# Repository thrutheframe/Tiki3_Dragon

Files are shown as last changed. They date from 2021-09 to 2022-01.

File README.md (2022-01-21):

Gen3 2 Orbiter Dragon 1
# Tiki3_Dragon
<b>Update 21 Nov 2022: </b> \
Till date, I had several requests to design the Tiki3 Dragon mount with a 4010/4020 fan to replace the 3010 fan that cools the hotend. The objective I set on Tiki3 mount system are ease of print, compact, light-weight and efficient. 
\
\
Looking at the side profile of the dragon or V6 hotend, the window needed to push air through is around 25mmx25mm = 625mm sq. For a 4010 the fan diameter is around 38mm which equates to an area of 1134mm sq. For a 3010 fan with a diameter of 28mm it is 616mm sq.
\
\
To install a 4010 fan. The reduction in air path is roughly 2:1. This would mean I have to include proper funneling to reduce the air path which result in the increase the width of the mount, making it not compact. So screw-it and make a short funnel. An axial fan produces low pressure air, when faced with drastic decrease in duct size, back pressure will be a problem. The motor will spin at a slower rpm due to resistance, making efficiency an issue. 
\
\
For a 3010 fan, the air path is roughly 1:1, hence no funneling needed. If there is a need to push more air through the heatbreak fins (using the HF version), a higher rpm fan is recommended ie. Gdstime sells 3010 fan 24V at 12,000 rpm or 8.4V at 20,000 rpm.
\
\
To conclude, I am not going to design Tiki3 Dragon to fit a 4010/4020 fan. 
\
\
<b>Update 12 Nov 2021: </b> This mount is for Orbiter V1.5. There will not be an update of Tiki3_Dragon for Orbiter V2.0. Why? https://github.com/thrutheframe/Tiki3_O2

<b>Update 17 Oct 2021: </b> included fan_duct V2 and added body_top and fanduct_bracket for adxl345. Please note the distance for the mounting holes are 19mm. you will also need to directly solder your wire or use L-pins.
\
\
<b>Update 27 Sep 2021: </b> I have included the step and stl file for the body_base.
\
\
<b>Update 12 Sep 2021: </b> shorter version of cable relief added. reduce by 20mm from the original. This is to prevent the cable from hitting the top bar during tall prints. 
\
\
<b>Update 11 Sep 2021: </b> The existing opening for the heater and thermistor cables enlarge slightly. Do note that if you orientate the heater block is the opposing direction. The opening should not be used. The wire will then run outside the BLT bracket and tied to the cable relief. 
\
\
\
\
<u> BOM of screw:\
-4pcs M3x12 or M3x14 for 3010 fan\
-2pcs M3x12 or M3x14 for fan duct (washer maybe needed as the slot are larger for horizontal adjustments)\
-2pcs M3x8 for body_base to ender carriage\
-2pcs M3x8 for cable relief\
-4pcs M3x8 for BL Bracket\
-1pc  M3x8 for fan duct bracket to body_top\
-2pcs M3x20 for mounting the orbiter and orbiter bracket to the body\
-4pcs M2.5x8 for dragon to Orbiter bracket (it should have come with the dragon)
\
\
BOM\
-3010 fan (Please use the high static pressure version, those that runs at 8500rpm will not push enough air)\
-5015 fan\
\
BLT offset: X= 35.5 Y=0

Please print in high temp filament. PLA and PLA+ will warp at the area closest to the heatblock. I print mine in CF petg. 

I have designed 2 sets; one for self-tapping M3 and another for M3x4x6.3 brass inserts. I recommend using the brass insert version if you can.

There are 2 versions for the mount. adxl and non-adxl. adxl is for Klipper users who want to install adxl1345. If you are a Marlin user, the non adxl version is better.

If printing in ABS or any material that will shrink, please remember to scale while slicing.

Holes on the self tap version are design at 3mm to accomodate for some shrinkage during print which will come to 2.8mm.

mount holes BLT bracket, fan duct bracket are slotted for 1-1.5mm for adjustments 

fanduct has a +-2mm vertical and +-0.7mm horizontal for adjustments 
\
\
  <b>CREDITS:</b>
I have to give credit where credit was due, so here goes: 
  
My wife, for putting up with me as I dive into this insanity of mine. 

20four80five: https://www.thingiverse.com/thing:3354741
For first planting the idea of a side mount cooling fan and front mount part cooling fan

Hangtight: https://www.thingiverse.com/thing:4725293
For using his fan duct in version 3.1 when I was still learning Fusion360 and basing some of the design from him work as they are good.

lorinczroby: https://www.thingiverse.com/thing:4725897
For designing the Orbiter which I used for the direct drive design.

Grabcad community for coming up with all the STEP files that I need ie; 5015, 4010, BL touch, etc

Mellow for sharing with me the STEP file of their NF-Zone hotend. 

Thingiverse and anyone/organisation that I forgot to give credit to.

Please do share your make on Thingiverse: https://www.thingiverse.com/thing:4949727

Gen3 2 Orbiter Dragon 3
Gen3 2 Orbiter Dragon 2
Gen3 2 Orbiter Dragon 4
Gen3 2 Orbiter Dragon 5

<b>FAQs:</b>

Q:Will this design be suitable for the E3D V6 mount?

A: No. This design is specifically rigid mounting the Phaetus Dragon Hotend (and its clones with the same mounting holes), Hence the name. 

Q: If No. Would you be adapt this design for the V6 hotend?

A: Not at the moment. One of the main reasion is that I do not use V6 mount. 

Q: Will this system fit the Sovol/Tronxy/TwoTrees etc etc?

A: Honestly, I would not know as I do not have those printers to work with.

Q: Would you release the STEP file for others to remix your design?

A: I asked this question once and the answer was "if u can remix it, u can design it on your own". He was kindof an asshole, but he was not wrong either. That is why I ended up designing my own mount system. I prefer not to be an asshole. Hence, I would release the STEP files for the body and BL bracket, which will be a good foundation to built your own version/remix. 

Q: Did you test print it in PLA? How did you get even get such specific numbers? "...I find stuff like this very misleading with serious potential to cause damage to printers when people try to do it..." 

A: I try my best to answer questions pertaining to the design. Constructive suggestions and contributions are greatly apperciated. Please be polite and nice.

Q: How accurate is the CFD simulation on your fan duct? Did u consider turbulance of of the 5015? Did u take into account of hotend movement? This design is misleading/shit/rubbish etc etc.

A: My basic CFD simulation of the particles movement (air) is to provide a validation that the air is directed under the nozzle when designing the fan duct. There are many other parameters that I would not know. tbh, it's a fanduct for 3D printer, not a cooling system of a nuclear plant... so take a chill pill and dun go karen/kevin on me. 

Q: Why do you add a heat sink to your motor? it is counter-productive as it add weight? 

A: Simple. I like it. 

Q: Why it is called Tiki3

A: Tiki was the name of our family dog. He passed away several years ago and we still miss him dearly. So I named this system after him. 

<b>Contributions</b>\
 My 3D printing hobby is running on Fun-Funds which is usually in fumes state. Contribution to this funds are from small print jobs, servicing 3D printers and the once-in-a-blue-moon tip to my paypal.me account. If you like using this system and would like to thanks me, a $2 coffee tip will be greatly appreciated (I like coffee). Thank you. https://www.paypal.com/paypalme/shannonheng

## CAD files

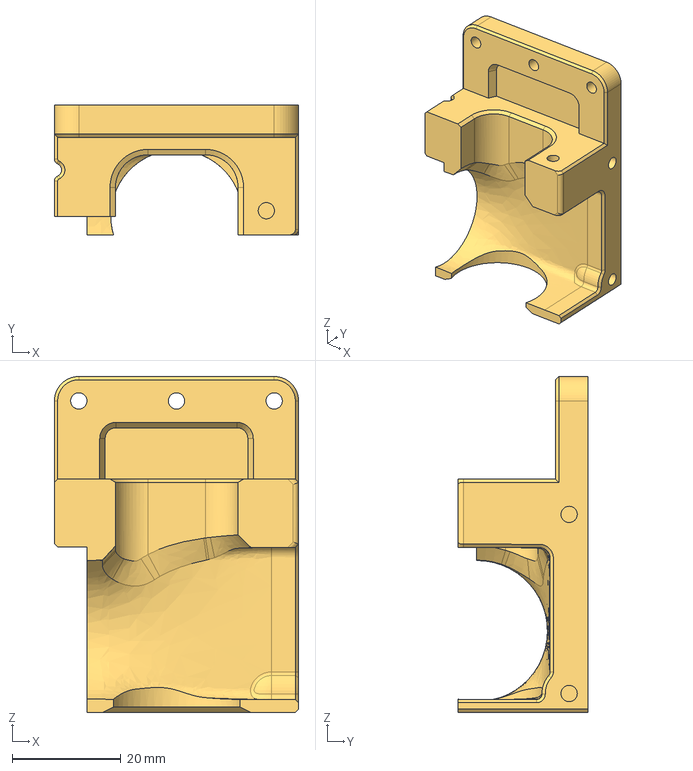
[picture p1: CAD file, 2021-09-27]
Body base STEP files/Tiki3 Dragon Body_base.step
45.0 x 24.0 x 61.9 mm

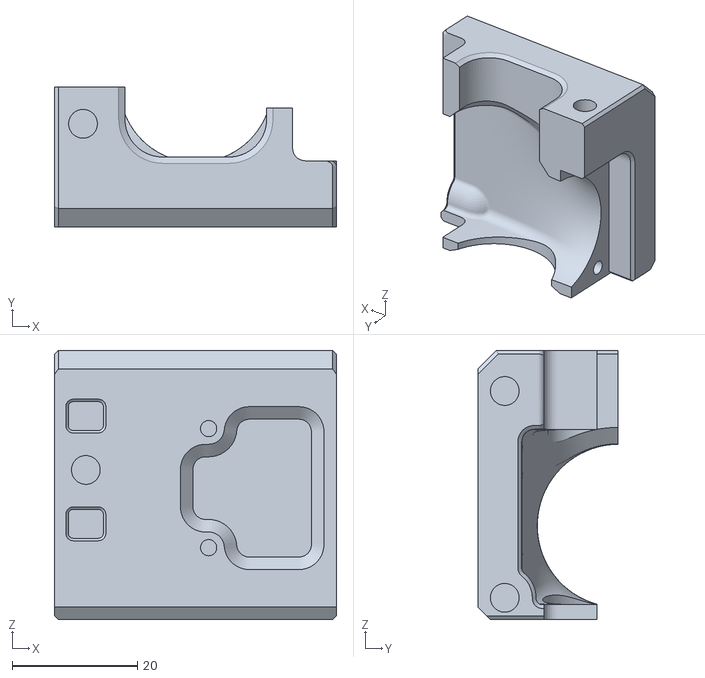
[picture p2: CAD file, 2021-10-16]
Tiki3 V3.2 Dragon brass insert/Brass insert Tiki3 Dragon Body_top adxl.stl
45.0 x 22.4 x 43.0

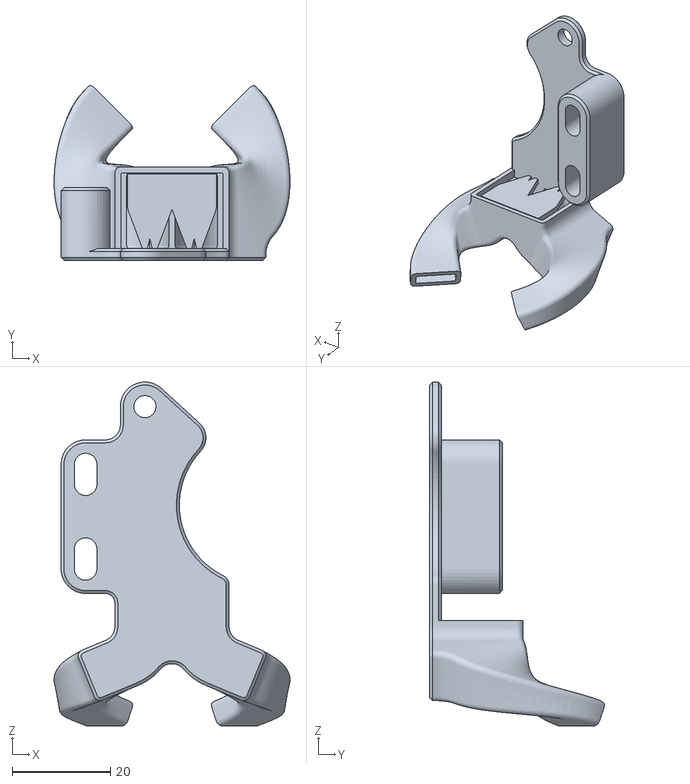
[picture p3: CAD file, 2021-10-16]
Tiki3 V3.2 Dragon other parts/Tiki3 Dragon Fan_duct V2.stl
47.9 x 35.5 x 69.9

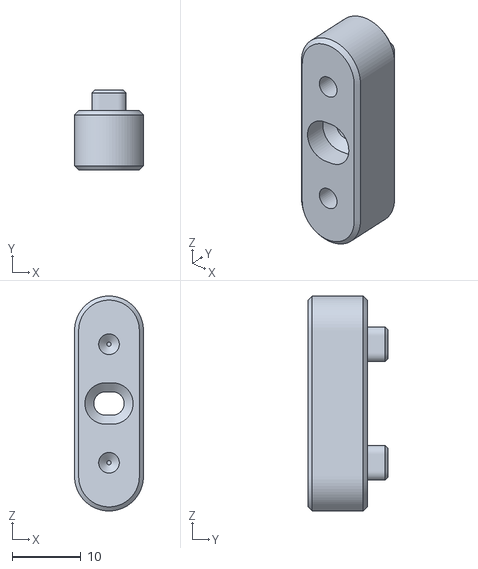
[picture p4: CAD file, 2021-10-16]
Tiki3 V3.2 Dragon self_tap/Tiki3 Dragon Fanduct bracket adxl.stl
10.00 x 11.6 x 31.2

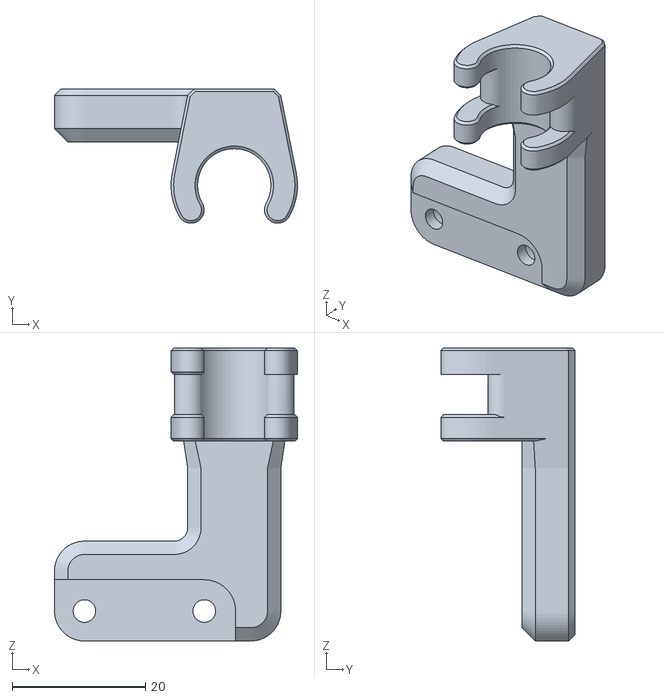
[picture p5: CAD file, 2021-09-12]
Tiki3 V3.2 Dragon other parts/Tiki3 Dragon Cable relief short ver.stl
36.5 x 20.2 x 44.0

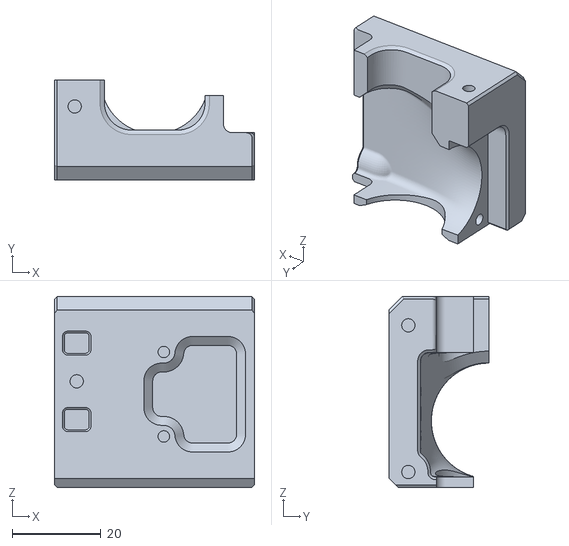
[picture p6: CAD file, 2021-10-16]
Tiki3 V3.2 Dragon self_tap/Tiki3 Dragon Body_top adxl.stl
45.0 x 22.4 x 43.0

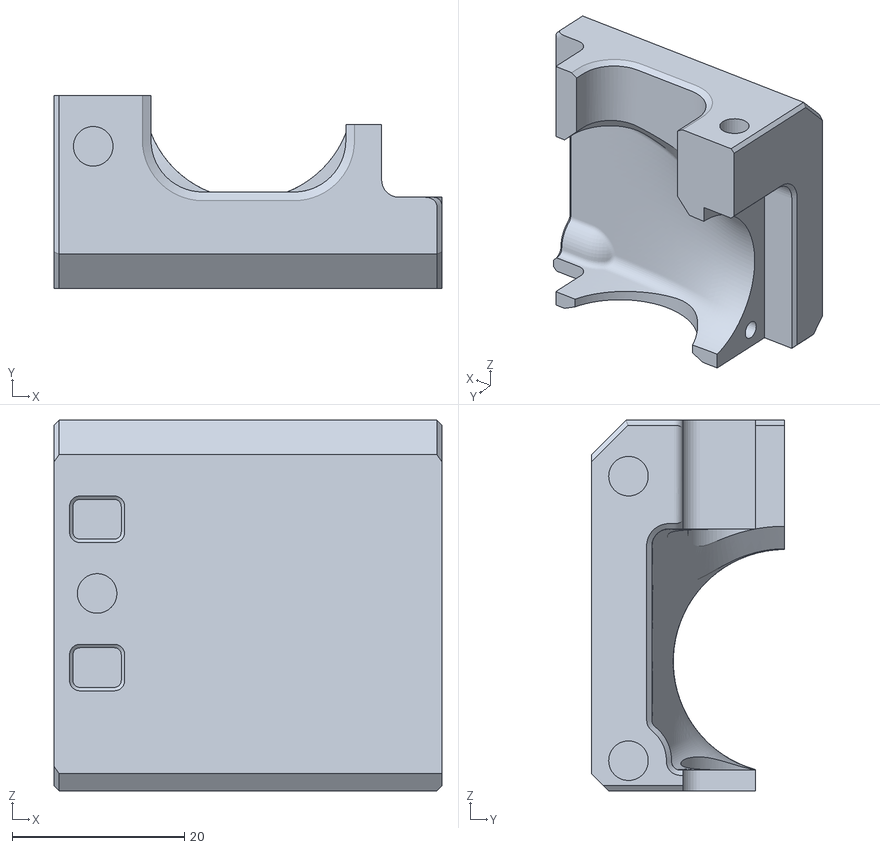
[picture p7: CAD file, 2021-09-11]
Tiki3 V3.2 Dragon brass insert/Brass insert Tiki3 Dragon Body_top.stl
45.0 x 22.4 x 43.0

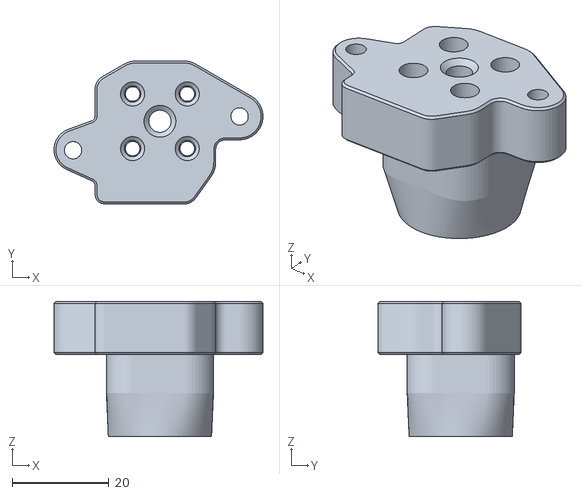
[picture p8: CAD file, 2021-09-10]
Tiki3 V3.2 Dragon other parts/Tiki3 Dragon Orbiter bracket.stl
43.3 x 29.6 x 28.0

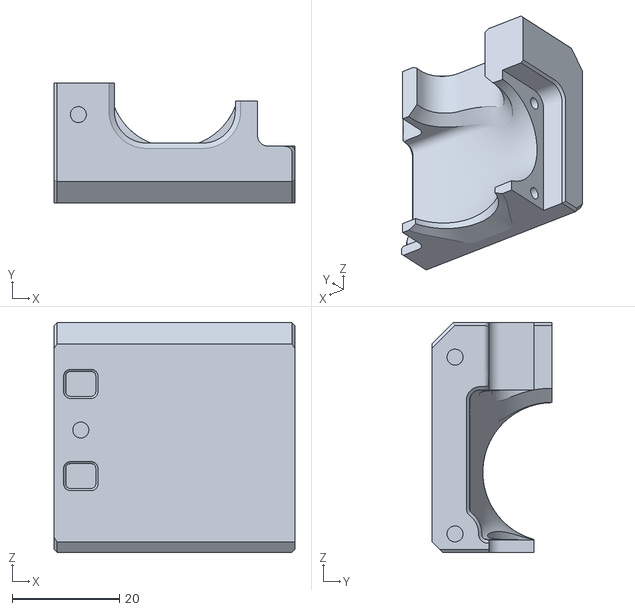
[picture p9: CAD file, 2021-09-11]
Tiki3 V3.2 Dragon self_tap/Tiki3 Dragon Body_top.stl
45.0 x 22.4 x 43.0

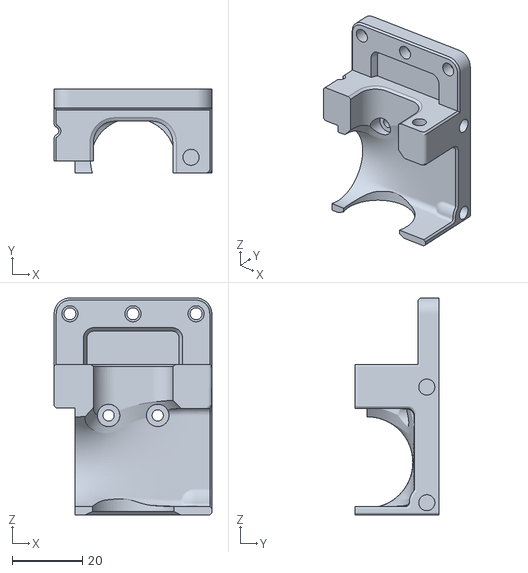
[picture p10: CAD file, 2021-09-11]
Tiki3 V3.2 Dragon brass insert/Brass insert Tiki3 Dragon Body_base.stl
45.0 x 24.0 x 61.9

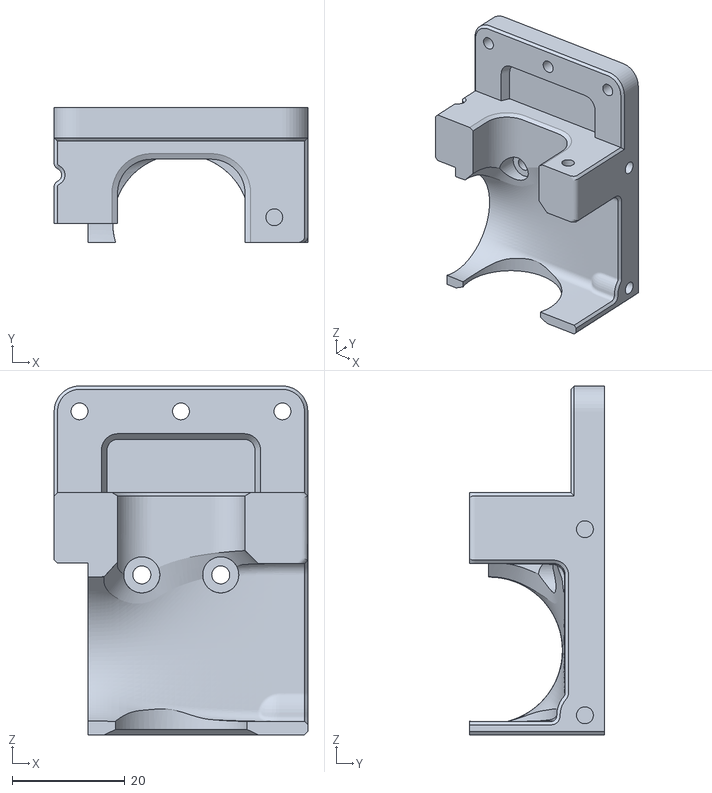
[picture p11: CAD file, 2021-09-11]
Tiki3 V3.2 Dragon self_tap/Tiki3 Dragon Body_base.stl
45.0 x 24.0 x 61.9

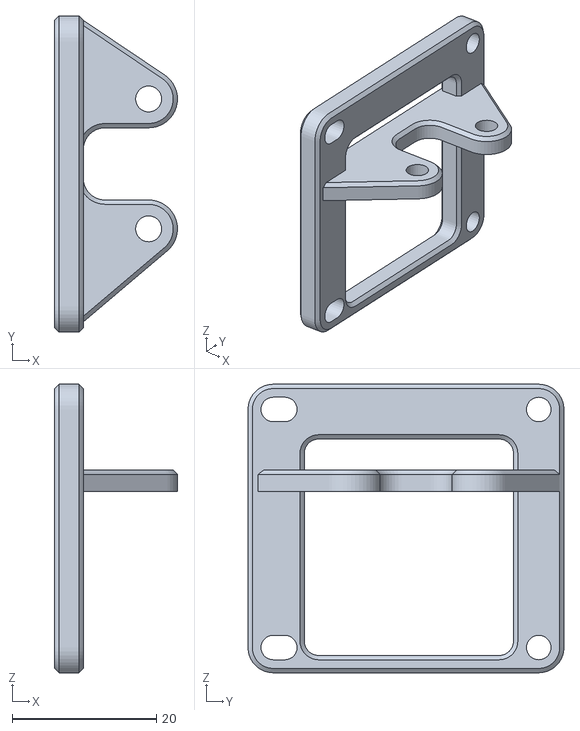
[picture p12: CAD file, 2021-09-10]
Tiki3 V3.2 Dragon other parts/Tiki3 Dragon BLT bracket.stl
17.0 x 43.8 x 40.0

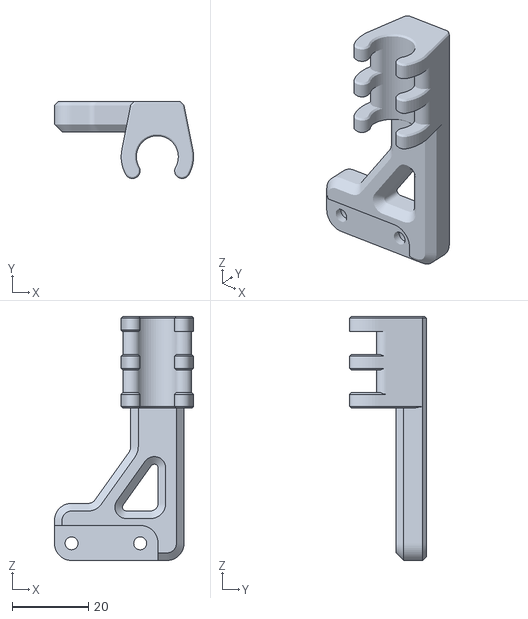
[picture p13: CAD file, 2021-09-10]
Tiki3 V3.2 Dragon other parts/Tiki3 Dragon Cable relief.stl
36.5 x 20.2 x 64.0

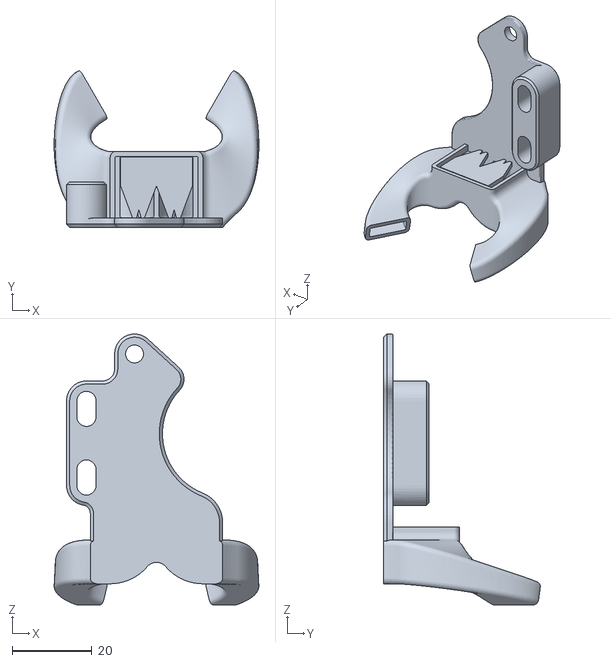
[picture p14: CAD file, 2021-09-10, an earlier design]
Tiki3 V3.2 Dragon other parts/Tiki3 Dragon Fan_duct.stl
51.3 x 39.3 x 67.9

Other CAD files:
Tiki3 V3.2 Dragon brass insert/Brass insert Tiki3 Dragon Fanduct bracket adxl.stl
Tiki3 V3.2 Dragon brass insert/Brass insert Tiki3 Dragon Fanduct bracket.stl
Tiki3 V3.2 Dragon self_tap/Tiki3 Dragon Fanduct bracket.stl

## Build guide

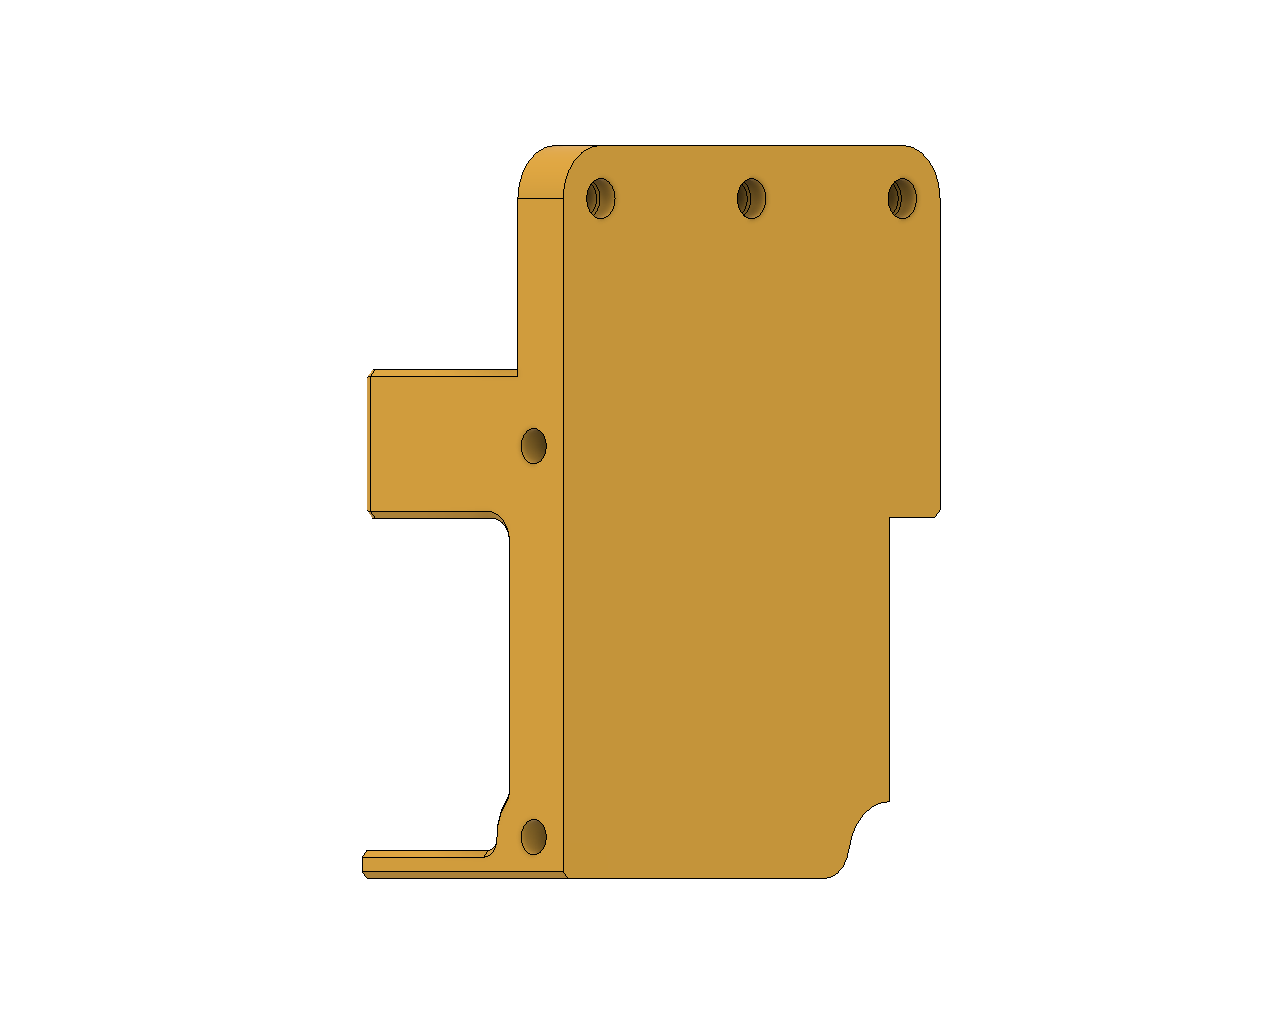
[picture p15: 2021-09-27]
Body base STEP files/Tiki3 Dragon Body_base 02.png

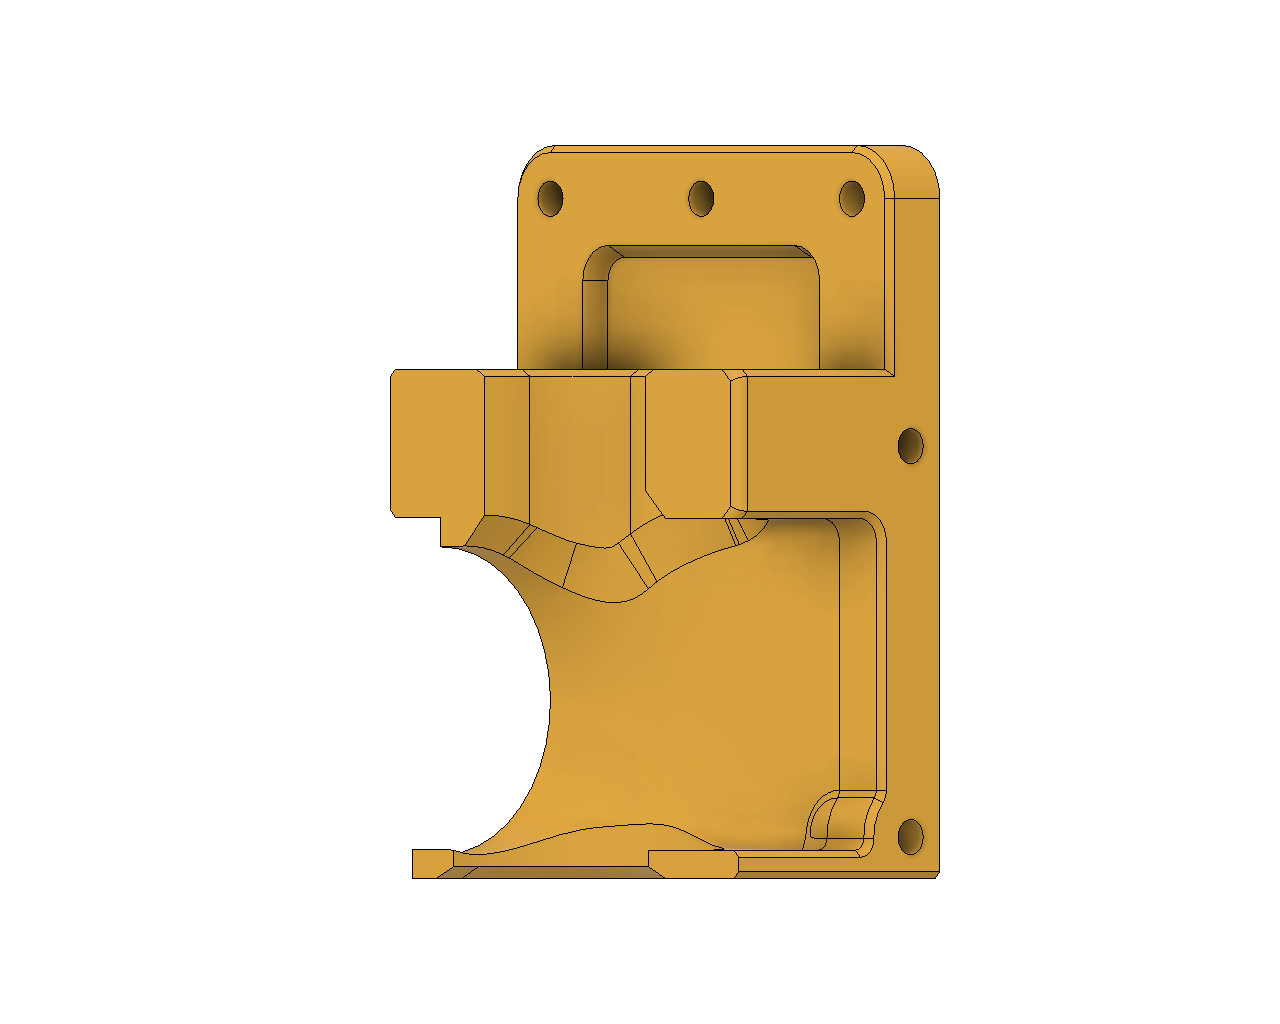
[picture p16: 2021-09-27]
Body base STEP files/Tiki3 Dragon Body_base 01.png

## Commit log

2021-09-11 enlarge opening for cables
    Enlarging the opening for the cables from heater and thermistor
    [Brass insert Tiki3 Dragon Body_base.stl, Brass insert Tiki3 Dragon Body_top.stl]
2021-09-11 enlarge opening for cables
    Enlarging opening for cables from heater and thermistor
    [Tiki3 Dragon Body_base.stl, Tiki3 Dragon Body_top.stl]
2021-09-12 short version
    [Tiki3 Dragon Cable relief short version.stl]
2021-09-27 Body_base step files
    [Tiki3 Dragon Body_base.step, Tiki3 Dragon Body_base.stl]
2021-10-16 adxl345 mount
    [Brass insert Tiki3 Dragon Fanduct bracket adxl.stl, Brass insert Tiki3 Dragon Body_top adxl.stl]
